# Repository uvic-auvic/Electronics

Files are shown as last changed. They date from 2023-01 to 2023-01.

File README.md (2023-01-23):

# Electronics
Repo containing schematics, pcb, gerber, and other documents for the Electrical Team.

# Directories

## Getting Started
Simple projects meant to introduce members to hardware design

## Submarine
Contains revisions and files for PCBs meant for the Submarine

## Test Equipment
Projects involving test equipment for the PCBs built for the Submarine.

# How revisions work for the projects
Each project will contain a release and development folder. The release folder will contain the board revision that has been ordered, while the development folder will contain revisions that have not been ordered. 

Revisions will be decided by level of change with regards to schematics and pcbs. PCB layout changes and varients will increment by 0.1 and schematic changes will increment by 1. For example, if the power board required a layout change due to a bad route, then the revisions would go from 1.0 to 1.1 because the schematics remain unchanged. If the schematics requried to be redone due to supply chain issues, then the revisions would go from 1.0. to 2.0.

All project revisions should contain a file outlining the reason for the changes for documentation purposes.

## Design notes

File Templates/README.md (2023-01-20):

# Templates
This folder contains template schematics that are common to many PCBs. To save development time, these schematics can be dragged and dropped into a project and modified as needed.

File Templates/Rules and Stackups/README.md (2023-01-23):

# Rules
This directory contains template rules to order boards from different PCB manufacturuers.

Credit to [Ayberk Özgür](https://github.com/ayberkozgur) for the JLC files.

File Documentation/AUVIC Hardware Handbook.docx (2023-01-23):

# Table Of Contents

Table Of Contents 1

General 3

Finding a part in the component library 3

Connectors 3

Resistors 4

Capacitors 4

Microcontroller 6

Microcontroller selection 6

Supporting Hardware 7

Debug 7

LED 9

Oscillator 9

Power Supply 10

Communications 12

Instructions for Creating a New Altium Project 14

Schematic and PCB file 14

PDF Export 14

Active BOM 14

Github and gitignore 14

PCB Layout 15

ESD Protection 15

CAN Connectors 15

TVS diodes: 15

Best Practices and Design Reviews 18

Schematic 18

PCB 18

Preparing to Order 19

References 20

# General

## Finding a part in the component library

The easiest way to find a part is to search by the AUVIC component ID. When searching by component ID, if there are multiple results, ensure that the latest revision is used. The 1 to 2 digit number after the last hyphen is the revision number. Component IDs listed in this document do not contain the revision number. The number will appear when searching in Altium.

# Connectors

Table 1 shows AUVIC’s standard connectors. It should be used whenever possible. Avoid using terminal blocks unless it benefits the design or the standard connectors are not satisfactory. When placing a parts order for your board, ensure that the other end of any connector used is also added to the order.

Standard Connectors List
Purpose | Description | Digikey Part Number | AUVIC Component ID | Price

Power
Power < 10A | Connector Header Through Hole, Right Angle 4 position 0.118" (3.00mm) | WM1820-ND | CMP-005-0021 | $2.24
Power < 5A | Connector Header Through Hole, Right Angle 2 position 0.118" (3.00mm) | WM1819-ND | CMP-00001 | $1.48
Power < 69A | Connector Header Through Hole, Right Angle 6 position 0.224" (5.70mm) | WM11971-ND | CMP-00049 | $3.50
Power < 92A | Connector Header Through Hole, Right Angle 8 position 0.224" (5.70mm) | WM11972-ND | CMP-00051 | $4.18

Data, Data + Power
2 Pin Data | Connector Header Through Hole, Right Angle 2 position 0.100" (2.54mm) | A33855-ND | CMP-00010 | $2.18
4 Pin Data, 2 Pin Data + Power < 2A | Connector Header Through Hole, Right Angle 4 position 0.100" (2.54mm) | A33860-ND | CMP-005-0029 | $1.63
3 Pin Data | Connector Header Through Hole, Right Angle 2 position 0.100" (2.54mm) | A32563-ND | CMP-00099-4 | $2.05

Table 1: Standard Connectors

# Resistors

1. Use SMD resistors unless absolutely necessary for the design
2. Use 0603 sized resistors for SMD unless the power dissipation requirements are higher. 0603 is small but still easy to solder. If we stick to a standard size, it becomes easier to keep resistors in stock
3. Use only 1% resistors unless a higher precision is required. In a production design, 5% would be used to save money since higher precision resistors cost more. However, since we only build a few boards, the cost savings does not outweigh the disadvantages. If all resistors in a board are the same tolerance, we don’t have to order multiple parts for the same resistance. It also becomes easier to keep resistors in stock.

# Capacitors

1. Use SMD capacitors unless absolutely necessary for the design. When using large capacitors (>100uF), you may choose to place multiple smaller capacitors in parallel instead of placing one large capacitor.
2. It is recommended to use 0603 and 0805 sizes for small value ceramic capacitors like bypass capacitors. Try to use the smaller of the two if you have an option.

Standard Capacitors List
Capacitor | Usage | AUVIC Component ID | Digi-Key PN
1nF Ceramic | Filters | CMP-00018 | 1276-1018-2-ND
150nF Ceramic | Bypass cap, filters | CMP-00020 | 1276-6476-1-ND
100nF Ceramic | Bypass cap, filters | CMP-00000 | 1276-1033-1-ND
1uF Ceramic | Bypass cap, filters | CMP-00005 | 1276-6470-1-ND
4.7uF | Bypass cap, filters | CMP-00019 | 1276-2789-1-ND
10uF Ceramic | Bypass cap, filters | CMP-00004 | 1276-6767-1-ND

Table 2: Standard Capacitors

# Microcontroller

This section details the hardware requirements if using a microcontroller in your design.

## Microcontroller selection

AUVIC has moved to using the same microcontroller for all designs with a few exceptions. This was done in an effort to simplify firmware development. The STM32F413xG has been determined to be the best controller to use. The table 3 lists the variants you can choose from for your design. ST provides an 81-pin package, but due to the complexity of the footprint, this variant should not be used for new designs.

Microcontroller List

General Purpose
MFG PN | Description | AUVIC Component ID | Digi-Key PN
STM32F413VGT6 | 100-pin LQFP, 1Mbyte Flash 320KB RAM 100 MHz CPU | CMP-00007
STM32F413RGT6 | 64-pin LQFP, 1Mbyte Flash 320KB RAM 100 MHz CPU | CMP-00006
STM32F413ZGT6 | 144-pin LQFP, 1Mbyte Flash 320KB RAM 100 MHz CPU

Special Purpose
STM32F429VGT6 | For high performance or special peripheral requirements only 100-pin LQPF, 1Mbyte Flash 256+4KB RAM 180 MHz CPU | CMP-00008
~~STM32F042F4P6TR~~ | ~~For simple boards only.~~ ~~32-bit 48MHz 16kB (16k x8) Flash 20-TSSOP~~ | | ~~497-19320-1-ND~~

Table 3: List of approved microcontrollers

## Supporting Hardware

### Debug

All boards need to have a debug header that will connect to a ST debugger. This is how we flash new firmware to the boards and attach a debugger to step through code. The header also has UART for debugging which must be connected to UART capable pins on the microcontroller. It is recommended to connect RX to PD9 and TX to PD8 since these pins are connected to the ST-Link VCP pins on the Nucleo board. However, this is not a hard requirement. Note that the SWCLK, SWDIO, SWO, and NRST connect to specific pins on the STM microcontroller you are using (check the datasheet to make sure you are connecting to the right pin). The 5V pin must be connected to the board’s internal 5V through a schottky diode. This allows the debugger to power the microcontroller. See figure 1 and table 4 for reference.

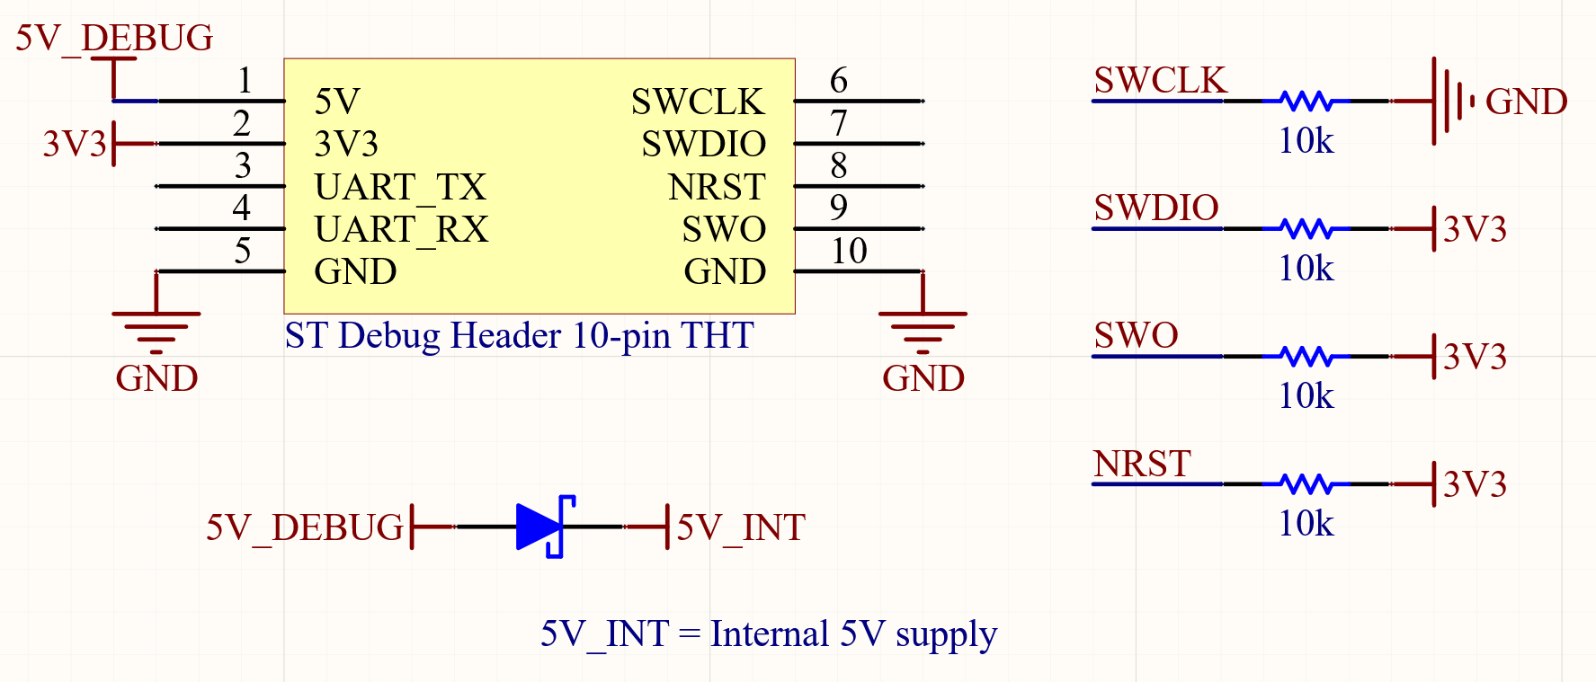
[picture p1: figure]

Figure 1: Microcontroller debug header schematic

Part | AUVIC Component ID
Header THT | CMP-00011
Header SMD | CMP-00013
Schottky Diode | CMP-057-0000
10kR Resistor | CMP-047-0013-1

Table 4: Microcontroller debug header component list

Another debug feature that all boards will have to incorporate are reset buttons to manually reset the STM microcontroller, and a boot header that allows the user to force the STM microcontroller into boot mode. See figure 2 and table 5 for reference.

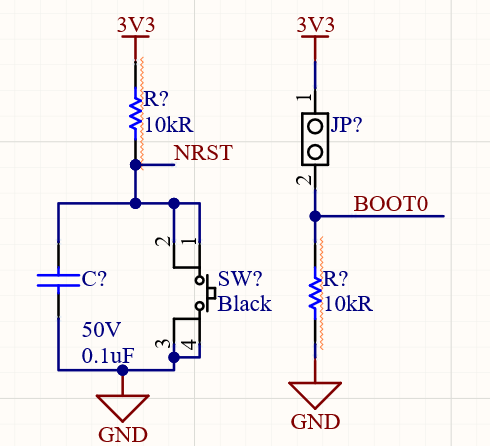
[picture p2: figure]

Figure 2: Microcontroller External Reset and Boot Schematic

Part | AUVIC Component ID
Switch SMD (option 1) | CMP-00077-1
0.1uF Capacitor | CMP-00000-3
2 pin Header | CMP-004-0001-1
10kR Resistor | CMP-047-0013-1
CMP-00104-1 (option 2) | CMP-00104-1

Table 5: Microcontroller External Reset and Boot component list

### LED

LEDs should be connected to the microcontroller’s GPIOs to help with debugging. The more LEDs the better, but 3 is the recommended number. It is recommended to connect the LEDs to PB0(green), PB7(blue), and PB14(red) since these pins are connected to LEDs on the Nucleo board. However, this is not a hard requirement. Use one red LED, one green LED and one blue LED. The table below shows the LED part number and recommended resistor values.

Part | AUVIC Component ID | Forward Voltage | Recommended Resistor, IF=4mA
| | | Vin = 3.3V | Vin = 5V | Vin = 12V | Vin = VBatt
Red LED | CMP-00066 | 2V | 330Ω | 750Ω | 2.49kΩ | 6.49kΩ
Green LED | CMP-00064 | 2.85V | 110Ω | 536Ω | 2.26kΩ | 6.34kΩ
Blue LED | CMP-00063 | 2.85V | 110Ω | 536Ω | 2.26kΩ | 6.34kΩ
Orange LED | CMP-00065 | 2V | 330Ω | 750Ω | 2.49kΩ | 6.49kΩ

Table x: LED component list and recommended resistor value

### Oscillator

If your design requires an accurate clock, you must add the circuit below to your schematic. For example, the motor controller’s RPM feedback requires an accurate clock because it compares the time between two rising edges of the motor back emf. However, if your board has space it is always recommended to add this so that the option of enabling it later is available. See figure 3 and table 5 for reference.

Part | AUVIC Component ID
8 Mhz Oscillator | CMP-00079-2
16pF Cap | CMP-00087-2

Table 5: Microcontroller oscillator component list

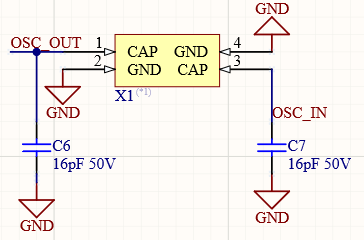
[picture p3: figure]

Figure 3: Microcontroller external oscillator schematic

### Power Supply

The STM microcontrollers can operate with a supply voltage of 1.8V to 3.6V [1]. AUVIC’s designs should operate the controllers using a 3.3V supply. It is recommended to use a 3.3V linear regulator with a input voltage of 5V. See figure X and table X for reference. All boards should take 5V from the power board’s 5V rail.

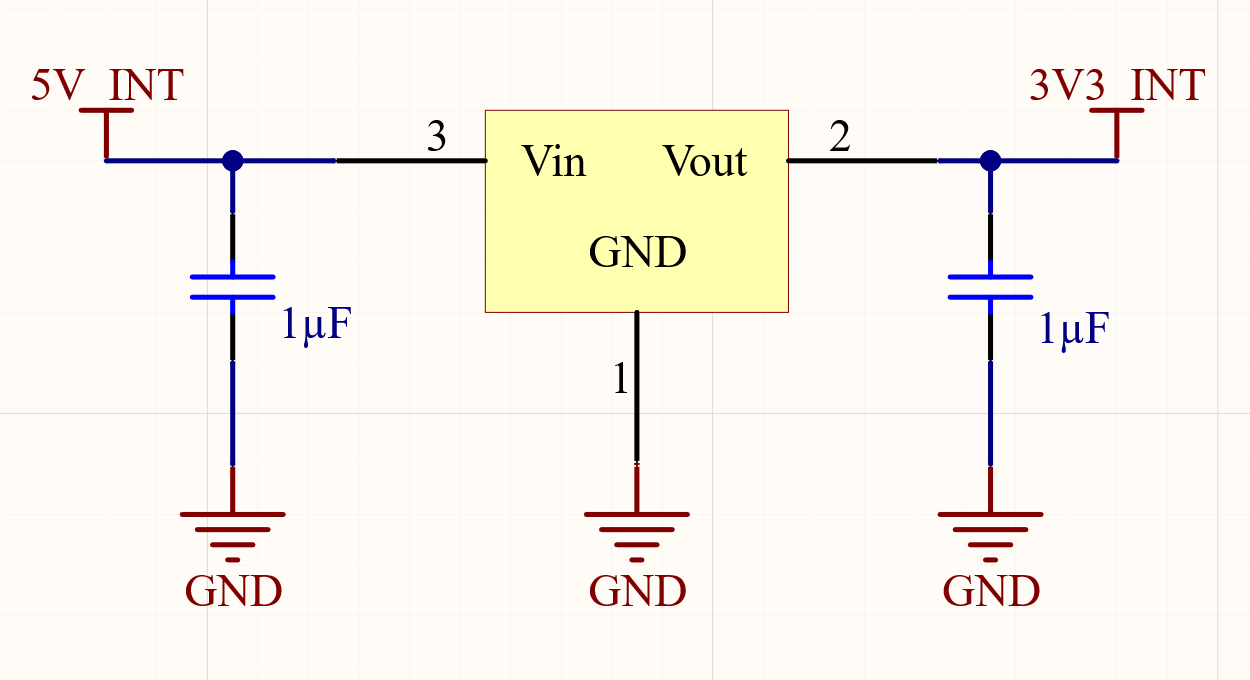
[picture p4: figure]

Part | AUVIC Component ID
LDO | CMP-00003
1uF Cap | CMP-00005

Table x: Component list for 3V3 rail

Figure x: Schematic for 3V rail

Appropriate bypass capacitors must be used.

- One 10uF ceramic or tantalum capacitor per chip
- One 0.1uF ceramic capacitor per VDD pin
- If VBAT is not being supplied by a separate battery, it should be connected to VDD with a 0.1uF ceramic decoupling capacitor. This will be the case for AUVIC’s boards unless we build a board with a built in battery.
- One 0.1uF and one 1uF ceramic capacitor per VDDA pin. 3.3V should be connected to the VDDA/VREF+ pin through a ferrite bead
- One 2.2uF low ESR ceramic capacitor per VCAP pin. There should be two VCAP pins. This is required if using the internal regulator on the microcontroller which is the case for AUVIC’s designs.

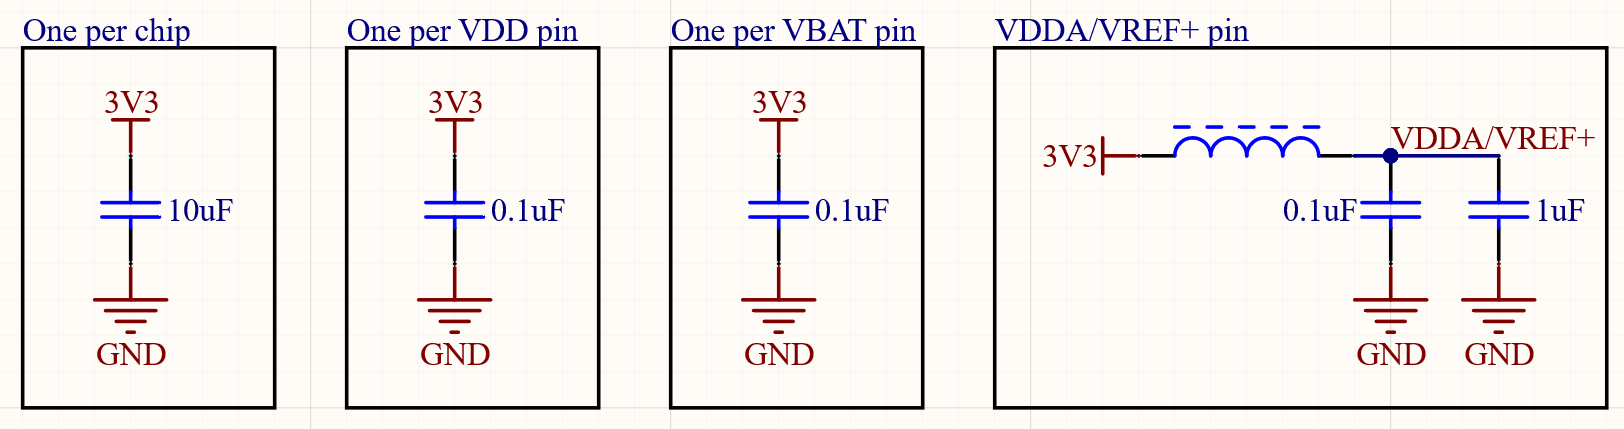
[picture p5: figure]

Figure xa: Microcontroller bypass capacitor schematic

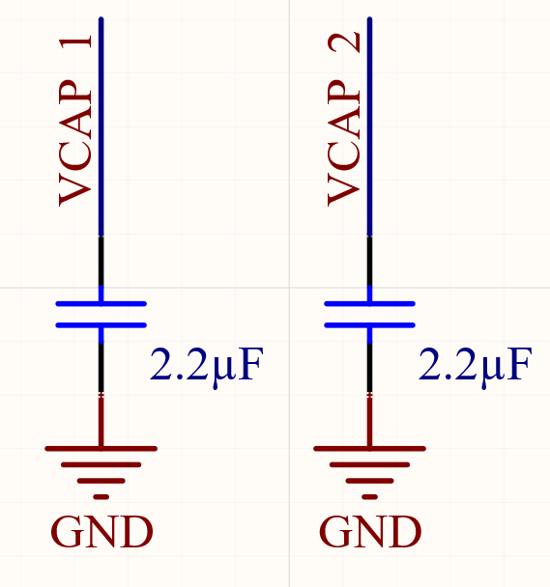
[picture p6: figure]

Part | AUVIC Component ID
0.1uF Cap | CMP-00000
1uF Cap | CMP-00005
10uF Cap | CMP-00004
Ferrite bead | CMP-00016
2.2uF Cap | CMP-006-0030

Table x: Microcontroller bypass capacitor component list

Figure xb: Microcontroller bypass capacitor schematic

For a more detailed explanation on the power supply requirements of the STM32F4 series microcontrollers, read cited text number 1.

## Communications

All AUVIC controllers will use CAN to communicate. CAN 2.0 operating at 500kbps will be used. See figure x for a reference design. The CAN_H and CAN_L lines must have a differential pair directive added in Altium to ensure the trace length on the PCB are the same. The CAN_TX and CAN_RX pins should be connected to CAN capable pins on the microcontroller. Choose CAN1 or CAN2 if possible. The CAN_STB pin should connect to a GPIO on the microcontroller. The 120Ω terminating resistor should be present in your schematic, but should only be populated if your component will be terminating the CAN bus. There will only be two devices per bus at either end of the bus. The TVS diode should be present in your schematic, but should not be populated unless deemed necessary after testing.

Note: This circuit is still under test and could change. A TVS diode and common mode choke might be added. Any board that uses this design should not be fabricated until this circuit has completed the required testing.

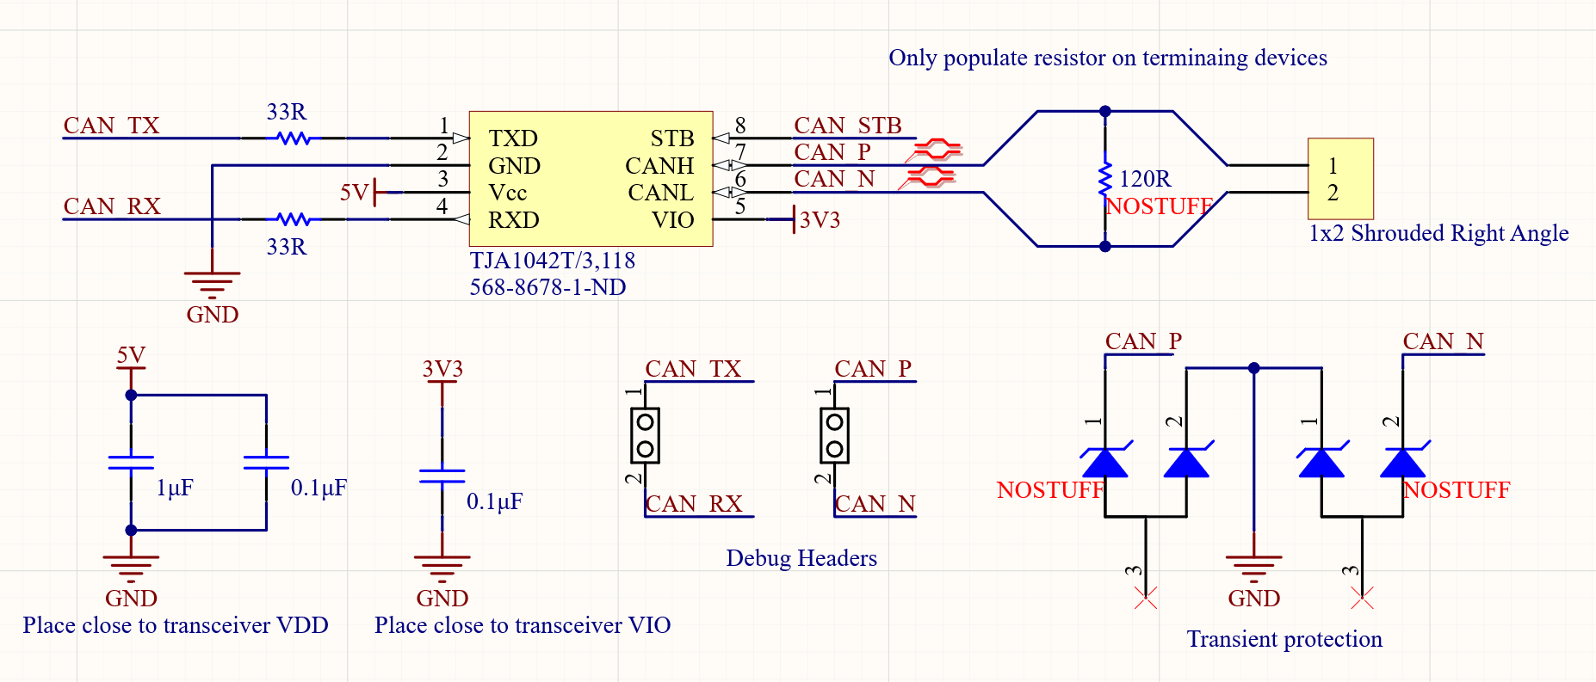
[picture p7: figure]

Figure x: CAN transceiver reference schematic

Part | AUVIC Component ID
CAN Transceiver | CMP-032-0000
2-pin Connector | CMP-00010
2-pin Header | CMP-004-0001
TVS Diode | CMP-058-0000
0.1uF | CMP-00000
1uF | CMP-00005
120 Ohm Resistor | CMP-00061
33 Ohm Resistor | CMP-00060

Table x: CAN transceiver schematic component list

# Instructions for Creating a New Altium Project

## Schematic and PCB file

## PDF Export

Use the same .OutJob file for everything. Naming convention.

## Active BOM

Currency, supplier part number under one column.

## Github and gitignore

Blah

Don’t upload history and project output files

# PCB Layout

The following sections will give recommendations for PCB layouts.

## ESD Protection

Electrostatic Discharge is the sudden flow of electricity between two charged objects. Testing for ESD on a prototype PCB requires the use of an ESD Gun, however these are expensive. The following subsections provide layout tips to lower the occurrence of ESD.

### CAN Connectors

AND8169/D EMI/ESD Protection Solutions for the CAN Bus by ON Semiconductor gives the following guidelines on ESD protection:

1. Locate the protection devices (TVS or diode) as close as possible to the I/O connector. This absorbs transient voltage before it couples to adjacent traces.
2. Minimize the loop area for the high-speed data lines, power and ground lines to reduce the radiated emissions and RF noise.
3. Minimize path length between CAN signal lines and protective devices.
4. Use ground planes whenever possible to reduce parasitic capacitance and inductance.

### TVS diodes:

Protects a transceiver by clamping a surge voltage to a safe level.

  - Pros: High Z below breakdown voltage and low Z above breakdown voltage. Optimized to absorb peak energy of transient voltages.
  - Cons: May clamp the CAN_L and CAN_H waveforms if a common mode or offset voltage exists.
  - Chosen TVS diode: PESD36VS2UT

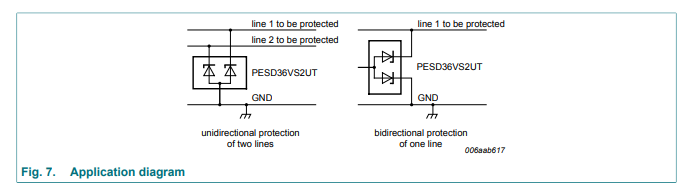
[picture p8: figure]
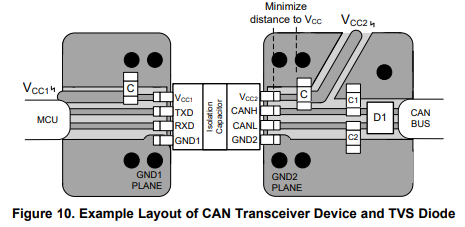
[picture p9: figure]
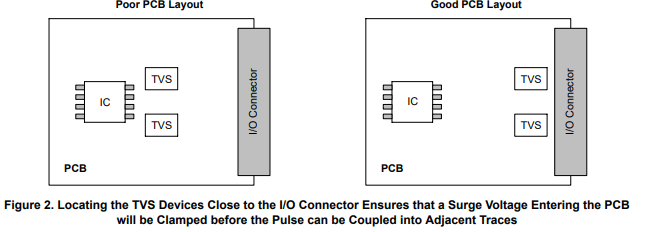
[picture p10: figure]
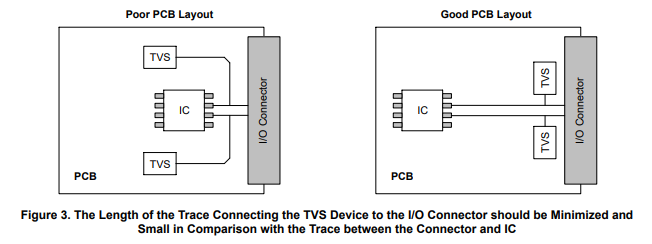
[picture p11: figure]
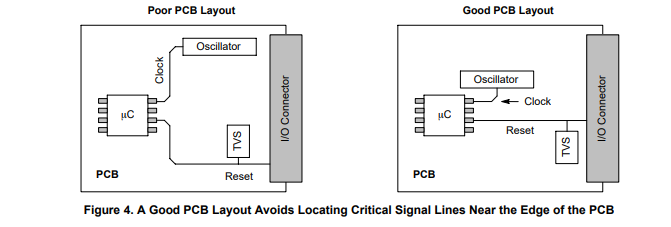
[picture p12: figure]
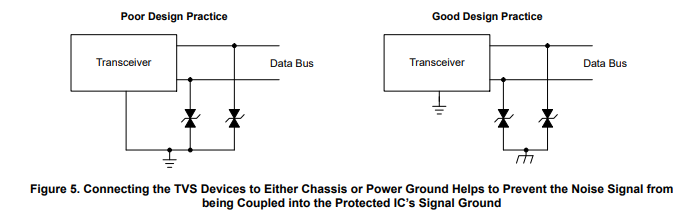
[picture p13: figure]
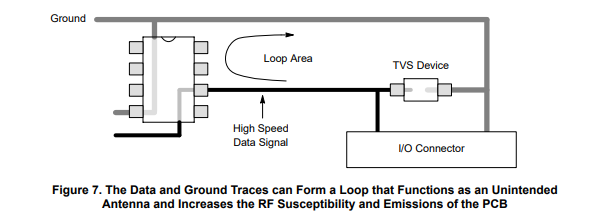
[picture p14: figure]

# Best Practices and Design Reviews

## Schematic

1. Be wary of logic levels on STM32 (5V tolerant etc)
2. Ensure correct resistors for LEDs

## PCB

4. Make sure vias are not directly under silkscreen designators or they will not print correctly
5. Use lower density component footprints
6. Double check bypass cap requirements for ICs
7. Place connectors at edge of board oriented away from center of board
8. Place designators so that when letters are upright the corresponding component is below
9. Vias: tent all vias and set to direct connect in thermal relief
10. Remove unnecessary bends in traces

https://www.ti.com/lit/an/szza009/szza009.pdf?ts=1610821093742&ref_url=https%253A%252F%252Fwww.google.com%252F

https://www.allaboutcircuits.com/technical-articles/practical-pcb-layout-tips/

https://www.allaboutcircuits.com/technical-articles/common-layer-stack-ups-for-a-four-layer-board/

https://resources.altium.com/p/top-5-pcb-design-guidelines-every-pcb-designer-needs-know

The above are good resources for PCB best practices

Set Design rules to the following:

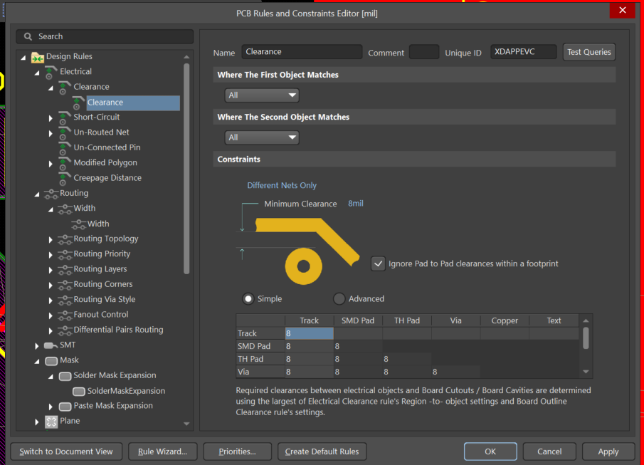
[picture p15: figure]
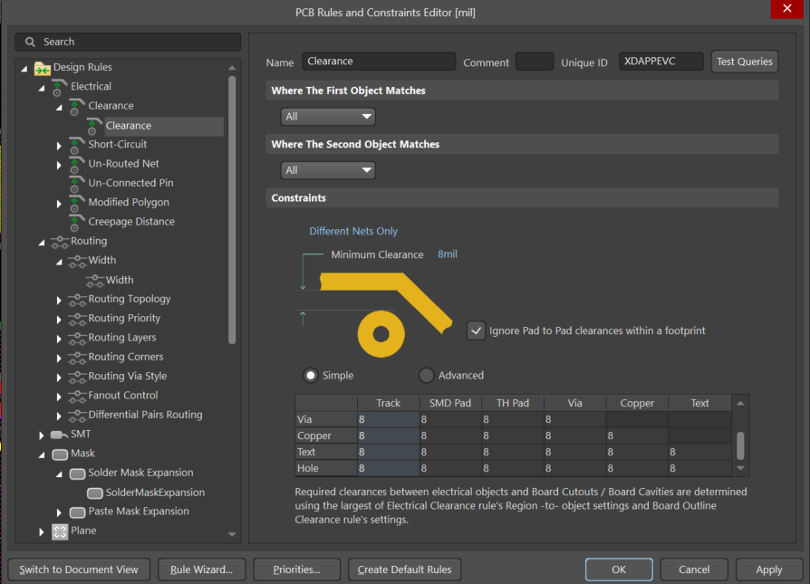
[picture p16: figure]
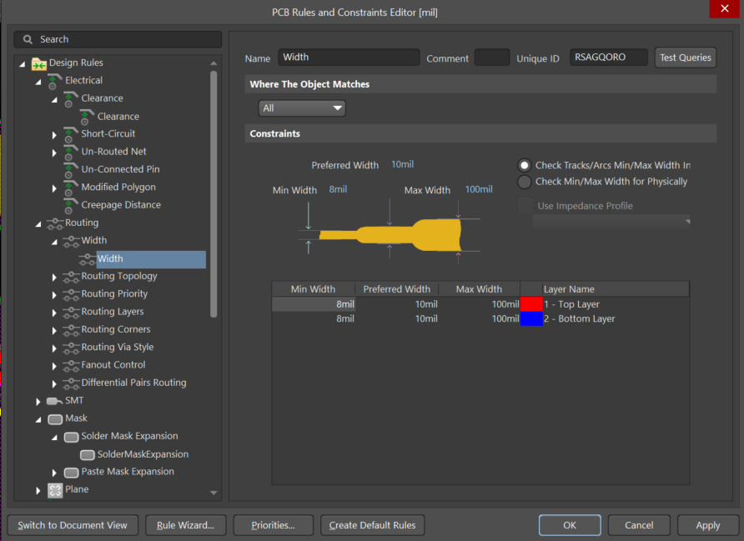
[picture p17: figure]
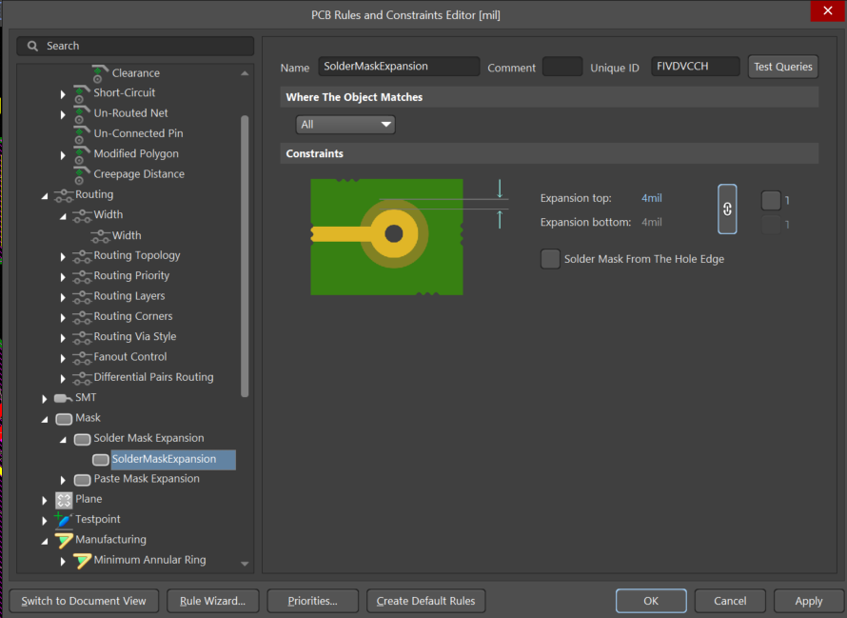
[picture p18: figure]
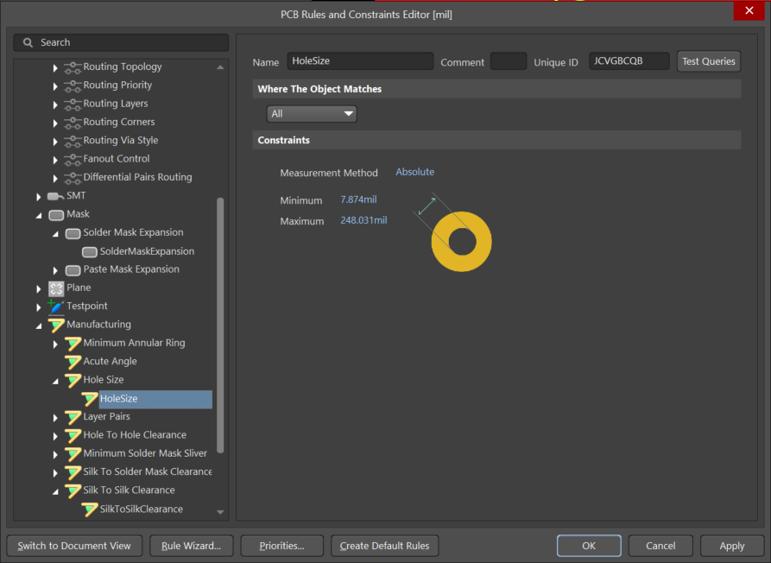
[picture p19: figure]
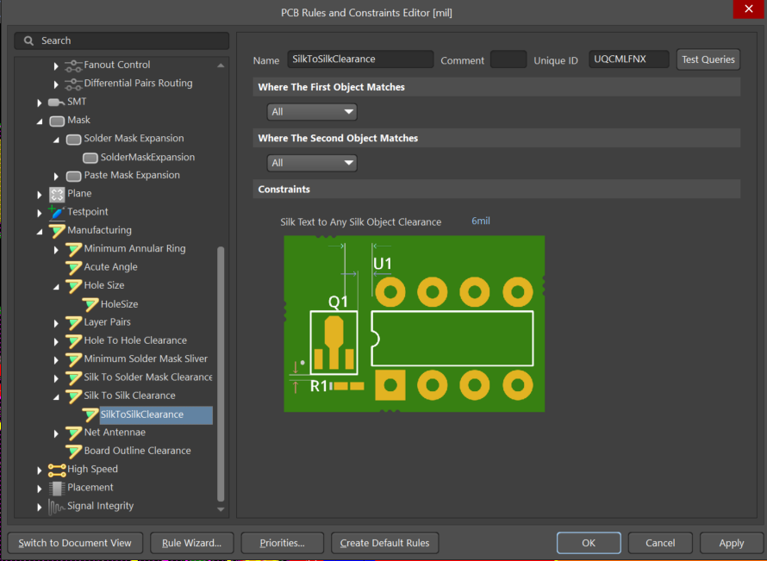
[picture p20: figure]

# Preparing to Order

1. Make a keepout layer
  a. Go to Keepout Layer (bottom tab)
  b. Draw lines around board edge
  c. Ensure polygon pours are in line with or greater than keepout area and repour
2. Open Settings folder-> Open Output Job Files -> Open PCBname.OutJob
3. Add New Output Container
  a. New Folder Structure
  b. Name it “Fabrication”
4. In Fabrication Outputs
  a. Add Gerber and NC Drill files and configure(by double clicking) based on instructions here: https://support.jlcpcb.com/article/42-how-to-export-altium-pcb-to-gerber-files
  b. *ignore drill drawing tab
5. Click enabled and link to Fabrication Folder
6. Add New Output Container
  a. New Folder Structure
  b. Name it “Step”
7. In Export Outputs
  a. Add Step file
8. Click enabled and link to Step Folder
9. Add New Output Container
  a. New Folder Structure
  b. Name it “BOM”
10. In Report Outputs
  a. Add Project BOM
11. Click enabled and link to Report Folder
12. Click generate content in all output containers

# References

[1] https://www.st.com/resource/en/application_note/dm00115714-getting-started-with-stm32f4xxxx-mcu-hardware-development-stmicroelectronics.pdf

[2]

https://assets.nexperia.com/documents/data-sheet/PESD36VS2UT.pdf

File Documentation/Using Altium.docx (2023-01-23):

# Using Altium

Work in Progress. The idea of this document is every time you have to look something up or figure out something with regards to using Altium, throw it in this document. In my opinion, Altium’s online documentation is pretty confusing and hard to follow. For example, they would say “do x from menu y” without explaining how to get to menu y. Because of this, we have this document to lay out how to do things in Altium outlined as simply as possible.

1. Shortcuts 1

2. Renewing the Team Altium License 1

2.1 Example Application Form 2

3. Schematic to PCB 4

Revision History 6

# 1. Shortcuts

Key Combination | Action
p | Open Place menu
j | Open find menu
Click on part of track then tab | Selects entire track
Ctrl+shift+scroll wheel | Change layers
Shift+Spacebar (while making polygon) | Change corner type

# 2. Renewing the Team Altium License

Author: Rob Keen

Must be done annually around the beginning of November. Complete the form at https://www.altium.com/solutions/academic-programs/team-sponsorships and you should get an email from Altium a few days later (method as of November 8th, 2021).

Important Note: Make sure the email in the registration form is one that is registered under an administrator in the Altium dashboard (https://dashboard.live.altium.com). This way, the existing license will get updated instead of needing to make a completely new workspace. If the existing workspace does not get updated, reach out to Altium. Can be checked through the above linked Altium dashboard.

University address for easy copy-pasting: 3800 Finnerty Rd, Victoria, CA V8P 5C2

## 2.1 Example Application Form

The following is an example completed form that resulted in a successful Altium sponsorship:

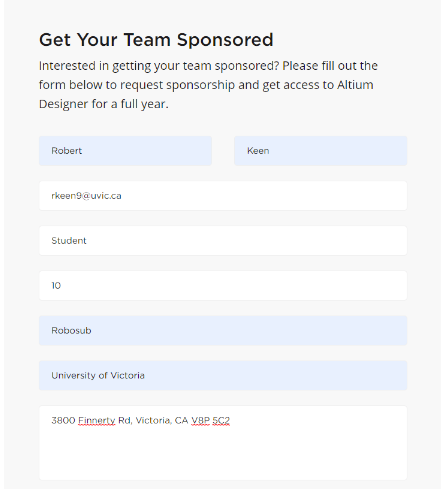
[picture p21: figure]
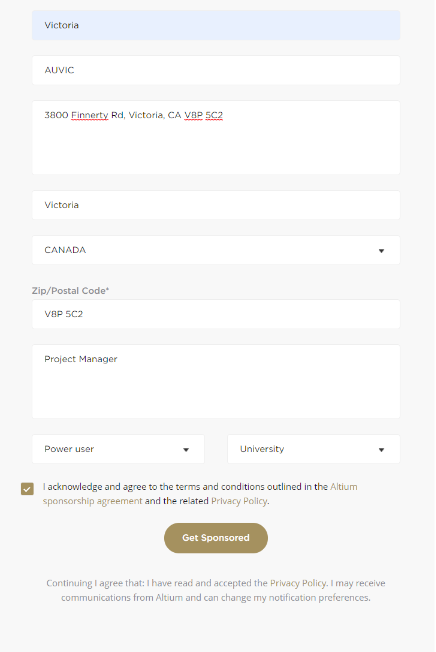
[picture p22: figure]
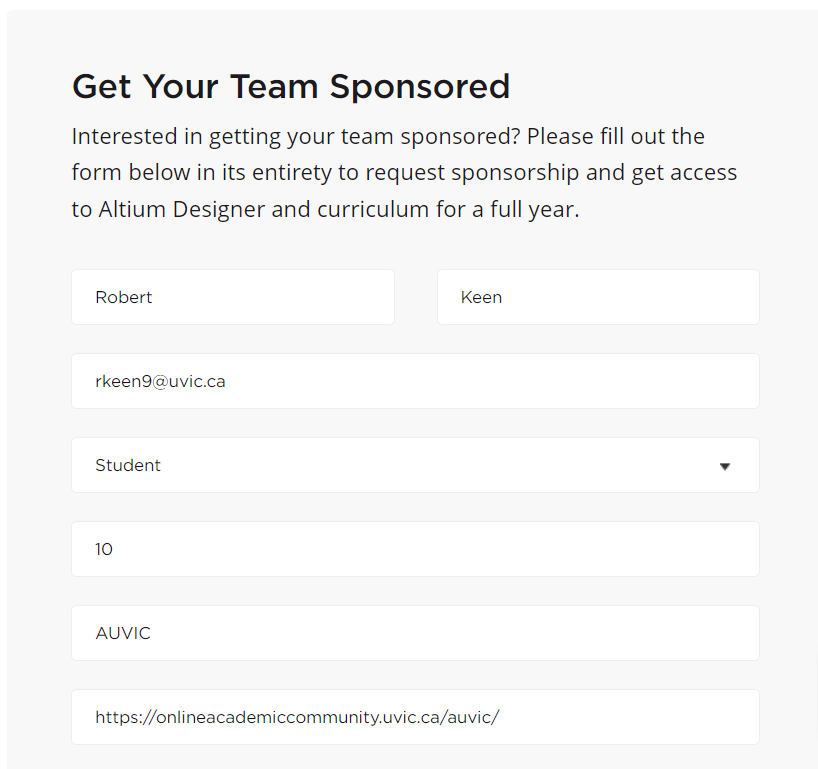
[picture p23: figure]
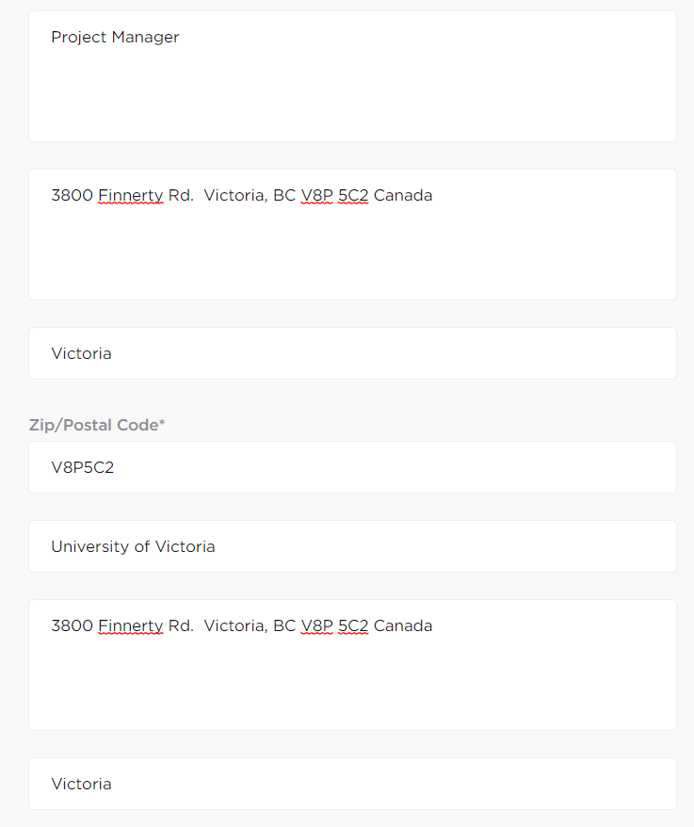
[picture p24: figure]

# 3. Schematic to PCB

Author: Rob Keen

1. Create new .PcbDoc file by right clicking on the project in the projects tab and choosing “Add New to Project>PCB”


2. Enter the new document, save with ctrl+s, and name the file whatever you want
3. “Design>Import changes From filename.PrjPcb”


4. From the Engineering Change Order window that appears, “Validate Changes” and address any errors that come up  Note: the above error can be safely ignored


5. Once errors are addressed click “Execute Changes”
6. You are now ready for routing

# 4. Differential Pair Routing

Author: Rob Keen

Sources: https://www.altium.com/documentation/altium-designer/pcb-dlg-managediffpairsformcreate-differential-pairs-from-nets-ad

## 4.1 Getting to the Differential Pair Editor

1. With the .PcbDoc file open, show the PCB panel by clicking “View>Panels>PCB”


2. Open the PCB panel, click the drop down menu at the top (by default it says “Nets”) and choose “Differential pairs Editor”


# Revision History

Name | Date | Revision Details
Robert Keen | Nov. 8, 2021 | Initial release
Robert Keen | Nov. 20, 2021 | Converted this document into a generic using Altium document

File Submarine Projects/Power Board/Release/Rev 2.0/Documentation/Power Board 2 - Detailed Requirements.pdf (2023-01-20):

## Overview

The Autonomous Underwater Vehicle Interdisciplinary Club (AUVIC) competes in an annual international competition where teams build autonomous underwater vehicles (AUVs) to complete an underwater obstacle course. AUVIC is in need of a new power and battery management board(PMB) for the 2021 Autonomous Underwater Vehicle (AUV).

## Specifications

The new PMB is divided into four subsections. The requirements for each subsection are outlined in the following sections.

## 3.1 Battery Management

The following specifications were established by AUVIC for the battery management section of the power board:
1. Should have a input voltage range of 18V to 28V.
2. Should use two 6 cell LiPo batteries as its power source.
3. Should have the ability to run the two batteries in parallel.
4. Each battery should have fuses. Regular sized automotive fuses are recommended.
5. Should have LEDs to indicate if the battery is connected.
6. Should have the ability to monitor battery pack voltage, individual cell voltage and pack current.

## 3.2 Power Distribution

The following specifications were provided by AUVIC for the power distribution section of the PMB:
1. Should have the following power outputs for external systems:
1.1. 5V at 8A.
1.1.1. LCD board - 4A*
1.1.2. Inertial Measurement Unit (IMU) - 500mA
1.1.3. Hydrophones - 250mA*
1.1.4. Torpedo 5V electronics - 250mA*
1.1.5. Motor controller 5V electronics - 250mA*
1.1.6. Buffer for unplanned boards - 2.75A
1.2. 12V at 8A.
1.2.1. Doppler Velocity Log (DVL) - 3A
1.2.2. Ball dropper and grabber arm - 3A*
1.2.3. Buffer for unplanned boards - 2A
1.3. 16V at 3A.
1.3.1. Nvidia Jetson TX2 and peripherals - 3A
1.4. VBatt (22.2V nominal) at 60A continuous.

1

1.4.1. Motor controller - 60A peak
1.4.2. Torpedo launcher - 30A for < 1s
2. Should be able to switch on/off all external power using the microcontroller.
3. Should have the ability to monitor current for each external power output.
4. Should have LEDs at each output to indicate if the output is on or off.
5. Should have fuses at each output. Regular sized automotive fuses are recommended.
* Estimated values.

## 3.3 Microcontroller & Communication

The following specifications were provided by AUVIC for the microcontroller and communication section of the power board:
1. Should use a STM32F413 microcontroller.
2. Should have a RS232 transceiver to communicate with an IMU.
3. Should have LEDs connected to the microcontroller for debugging and to show system status.
4. Should use a Controller Area Network (CAN) bus to communicate to external systems.

## 3.4 Sensors

From AUVIC, the following requirements were given for the sensors section of the power board:
1. Should connect to a reed switch to power on/off the AUV.
2. Should connect to a water sensor to detect leaks in the vehicle’s housing.
3. Should measure internal pressure, temperature, and humidity.
4. Should connect to an external water pressure sensor used to determine the AUV’s depth in the water.

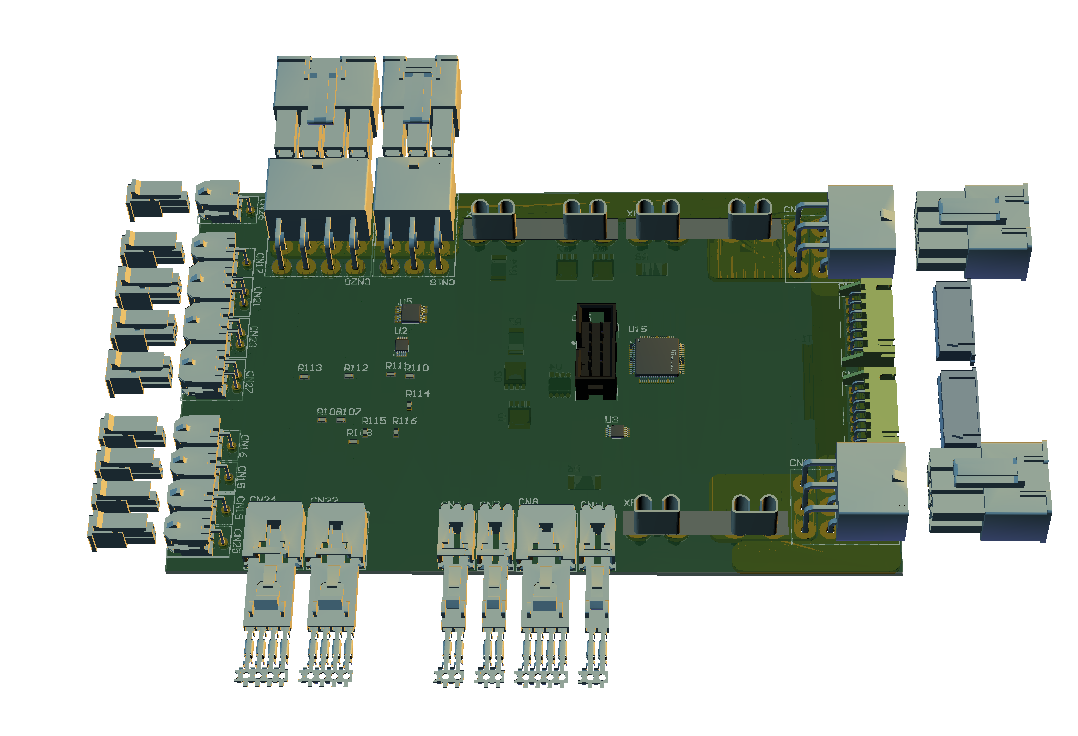
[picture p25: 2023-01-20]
Submarine Projects/Power Board/Release/Rev 2.0/3D Model/Power_Board_2.png

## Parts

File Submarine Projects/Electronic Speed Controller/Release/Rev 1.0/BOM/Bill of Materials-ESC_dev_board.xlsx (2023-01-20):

Line # | Name | Description | Designator | Revision ID | Revision State | Quantity | Manufacturer 1 | Manufacturer Part Number 1 | Manufacturer Lifecycle 1 | Supplier 1 | Supplier Part Number 1 | Supplier Unit Price 1 | Supplier Subtotal 1
 | 1μF | Capacitor, Ceramic, 50V, +/- 10%, 0603 SMD, X5R | C5 |  | Not managed | 1 | Samsung | CL10A105KB8NNNC | Volume Production | Digi-Key | 1276-1860-1-ND | 0.17 | 0.17
 | 0.1uF, 50V, 10%, X7R, 0603 | 0.1µF ±10% Ceramic Capacitor X7R 0603 (1608 Metric) | C6 |  | Not managed | 1 | TDK | C1608X7R1H104K | Not Recommended for New Design | Digi-Key | 445-1314-1-ND | 0.12 | 0.12
 | 100µF | 100µF 35V Aluminum Polymer Capacitor Radial, Can - SMD 30mOhm 2000 Hrs @ 105°C | C7, C8, C9, C10 |  | Not managed | 4 | Wurth Electronics | 875115652007 | Unknown | Digi-Key | 732-11942-1-ND | 2.76 | 11.04
 | Header Male 1x4 | 1x4, Pads Pitch: 0.1" (2.54mm), Through hole | CN3, CN4 |  | Not managed | 2 | Harwin | M20-9990446 | Volume Production | Digi-Key | 952-2266-ND | 0.19 | 0.38
 | 3x1, Terminal Block, Pitch: 5mm, Screw, THT | 3x1, Terminal Block, Pitch: 5mm, Screw, THT | CN5 |  | Not managed | 1 | Phoenix Contact | 1935174 | Volume Production | Digi-Key | 277-1578-ND | 0.6 | 0.6
 | 2x1 Term Block |  | J3 |  | Not managed | 1 | Phoenix Contact | 1935776 | Volume Production | Digi-Key | 277-6405-ND | 0.49 | 0.49
 | SI7625DN-T1-GE3 | P-Channel 30V 35A (Tc) 3.7W (Ta), 52W (Tc) Surface Mount PowerPAK® 1212-8 | Q1, Q2, Q3 |  | Not managed | 3 | Vishay Siliconix | SI7625DN-T1-GE3 | Volume Production | Digi-Key | SI7625DN-T1-GE3CT-ND | 1.07 | 3.21
 | SIS476DN-T1-GE3 | N-Channel 30V 40A (Tc) 3.7W (Ta), 52W (Tc) Surface Mount PowerPAK® 1212-8 | Q4, Q5, Q6 |  | Not managed | 3 | Vishay | SIS476DN-T1-GE3 | Volume Production | Digi-Key | SIS476DN-T1-GE3CT-ND | 1.12 | 3.36
 | 0R | 0R, 1%, 1/10W, 0603 SMD | R3, R4, R5, R6, R7, R8 |  | Not managed | 6 | Yageo | RC0603JR-070RL | Volume Production | Digi-Key | 311-0.0GRCT-ND | 0.019 | 0.19
 | 0.01 | RES 0.01 OHM 1% 3W 2512 | R9 |  | Not managed | 1 | Bourns | CRA2512-FZ-R010ELF | Unknown | Digi-Key | CRA2512-FZ-R010ELFCT-ND | 0.69 | 0.69
 | A4963 | A4963, BLDC, 3 Phase, Sensorless | U3 |  | Not managed | 1 | Allegro MicroSystems | A4963GLPTR-T | Volume Production | Digi-Key | 620-1686-1-ND | 2.7 | 2.7

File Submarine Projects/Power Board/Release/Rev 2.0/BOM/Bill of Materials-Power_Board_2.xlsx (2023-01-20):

Line # | Name | Description | Designator | Quantity | Manufacturer 1 | Manufacturer Part Number 1 | Manufacturer Lifecycle 1 | Supplier 1 | Supplier Part Number 1 | Supplier Unit Price 1 | Supplier Subtotal 1
 | CL10B104JB8NNNC | CAP CER 0.1UF 50V X7R 0603 | C1, C2, C3, C4, C5, C6, C8, C16, C22, C23, C32, C38, C39, C41, C42, C47, C49, C50, C51, C53, C60, C64, C66, C67, C68, C69, C70, C71, C74, C75, C76, C77, C78, C79, C80, C81, C82, C83, C84, C85, C86, C87, C88, C89 | 44
 | CL31B106KBHNNNE | Cap Ceramic 10uF 50V X7R 10% Pad SMD 1206 125°C T/R | C7, C24, C25, C26, C27, C40, C46, C52, C72 | 9
 | CL31B475KBHNNNE | Capacitor 4.7 uF 50 VDC PU=2000 ST, CL31B475KBHNNNE, Samsung | C9, C10, C21, C37 | 4 | Samsung | CL31B475KBHNNNE | Volume Production | Digi-Key | 1276-2789-1-ND | 0.38374 | 1.53
 | 470nF, 50V, 10%, 0603, Ceramic, SMD | Capacitor, Ceramic, 50V, 10%, 0603 SMD, X7R | C11, C28 | 2 | TDK | C1608X7R1H474K080AC | Volume Production | Digi-Key | 445-5952-6-ND | 0.26256 | 0.52512
 | CL10B102KB8NNNC | Cap Ceramic 0.001uF 50V X7R 10% Pad SMD 0603 125°C T/R | C12, C18, C29 | 3
 | GRM188R60J226MEA0D | MURATA - GRM188R60J226MEA0D - SMD Multilayer Ceramic Capacitor, 22 µF, 6.3 V, 0603 [1608 Metric], ± 20%, X5R, GRM Series | C13, C14, C19, C20 | 4
 | CL10C101FB8NNNC | Ceramic capacitor SMD 0603 100 pF 50 V 1 % | C15 | 1
 | CL21B154KBFNNNG | CAP CER 0.15UF 50V X7R 0805 | C17, C33 | 2
 | GRM1885C2A271JA01D | CAP CER 270PF 100V C0G/NP0 0603 | C30 | 1
 | C3216X5R1E476M160AC | TDK - C3216X5R1E476M160AC - SMD Multilayer Ceramic Capacitor, 47 µF, 25 V, 1206 [3216 Metric], ± 20%, X5R, C Series | C31, C35, C36 | 3
 | CGA4C2C0G1H272J060AA | CAP CER 2700PF 50V C0G 0805 | C34 | 1
 | GRM32ER71E226ME15K | CAP CER 22UF 25V X7R 1210 | C43, C44, C48 | 3
 | CL21B105KBFNNNG | SAMSUNG ELECTRO-MECHANICS - CL21B105KBFNNNG - MLCC CAPACITORS | C45, C65, C73 | 3
15 | 0.015uF 50V 0603 SMD, Ceramic | Capacitor, Ceramic, 50V, +/-10%, 0603 SMD, X7R | C54 | 1
2 | 4.7uF 50V 1206 SMD, Ceramic | Capacitor, Ceramic, 50V, +/- 10%, 1206 SMD, X7R | C55 | 1
5 | 1uF 25V 0603 SMD, Ceramic | Capacitor, Ceramic, 25V, +/- 10%, 0603 SMD, X5R | C56, C57 | 2 | Murata | GRM188R61E105KA12D | Volume Production | Digi-Key | 490-3897-1-ND | 0 | 0
4 | 0.1uF, 50V, 10%, X7R, 1608 | CAP CER 0.1UF 50V 10% X7R 1608 (0603) | C58 | 1 | Samsung | CL10B104KB8SFNC | Volume Production | Digi-Key | 1276-1936-1-ND | 0.10098 | 0.10098
6 | 10uF 10V 0805 SMD, Ceramic | Capacitor, Ceramic, 10V, +/- 10%, 0805 SMD, X5R | C59 | 1 | Murata | GRM219R61A106KE44D | Not Recommended for New Design | Digi-Key | 490-4735-1-ND | 0 | 0
 | 16pF Ceramic 50V 5% 0603 | Cap Ceramic 16pF 50V C0G 5% SMD 0603 125C Paper T/R | C61, C62 | 2
 | 2.2uF, 50V, 0603 SMD, X5R, Ceramic | Capacitor, Ceramic, 50V, 10%, 0603 SMD, X5R | C63 | 1 | Murata | GRM188R61H225KE11D | Volume Production | Digi-Key | 490-10733-6-ND | 0.38374 | 0.38374
 | 76825-0006 | CONNECTOR, HEADER, 6POS, 2ROW, 5.7MM; Product Range:Mega-Fit 76825 Series; Contact Termination Type:Through Hole; Gender:Header; No. of Contacts:6; Pitch Spacing:5.7mm; Contact Plating:Tin Plated Contacts; Contact Material:Copper | CN1, CN2, CN18 | 3 | Molex | 76825-0006 | Volume Production | Digi-Key | WM11971-ND | 2.39 | 7.18
 | S7B-XH-A(LF)(SN) | CONN HEADER XH SIDE 7POS 2.5MM | CN3, CN4 | 2 | JST | S7B-XH-A(LF)(SN) | Volume Production | Digi-Key | 455-2240-ND | 0.45443 | 0.90886
 | ST Debug Header 10-pin THT | CONN HEADER VERT 10POS 2.54MM | CN5 | 1 | Sullins | SBH11-PBPC-D05-ST-BK | Volume Production | Digi-Key | S9169-ND | 0.42413 | 0.42413
 | 1x2 Shrouded Right Angle | 02 MTE HDR SRRA LATCH | CN6, CN7, CN11 | 3 | TE Connectivity | 5-104935-5 | Volume Production | Digi-Key | A33855-ND | 1.47 | 4.42
 | Header, Male, 1x4, RA, Pitch 0.1" (2.54mm) | Connector Header Through Hole, Right Angle 4 position 0.100" (2.54mm) | CN8, CN22, CN24 | 3 | TE Connectivity | 5-104935-1 | Volume Production | Digi-Key | A33860-ND | 1.65 | 4.94
 | Header, Female, 1x2, Right Angle, Pitch 0.118" (3.00mm), THT | Connector Header Through Hole, Right Angle 2 position | CN15, CN16, CN17, CN19, CN25, CN26 | 6 | Molex | 43045-0202 | Volume Production | Digi-Key | WM1819-ND | 1.49 | 8.97
 | 76825-0008 | MOLEX 76825-0008. CONNECTOR, HEADER, 8POS, 2ROW, 5.7MM | CN20 | 1 | Molex | 76825-0008 | Volume Production | Digi-Key | WM11972-ND | 2.86 | 2.86
 | Header, Female, 2x2, RIght Angle, Pitch: 0.118" (3.00mm), THT | Connector Header Through Hole, Right Angle 4 position 0.118" (3.00mm) | CN21, CN23, CN27 | 3 | Molex | 0430450402 | Volume Production | Digi-Key | WM1820-ND | 2.26 | 6.79
 | LT Q39G-Q1OO-25-1 | LED GREEN DIFFUSED 0603 SMD | D1, D2, D4, D5, D6, D7, D11, D12, D13, D14 | 10 | Osram Opto | LT Q39G-Q1OO-25-1 | Volume Production | Digi-Key | 475-3442-1-ND | 0.2767 | 2.77
 | LED, 0805 (2012), Orange, Clear | LED, 0805 (2012), Orange, Clear | D3 | 1
17 | RB060M-60TR | Diode, Schottky, 60V, 2A | D8 | 1 | Rohm | RB060M-60TR | Volume Production | Digi-Key | 846-RB060M-60CT-ND | 0.43423 | 0.43423
 | DSS14UTR | Diode, Schottky, 40V, 1A | D9, D10 | 2 | Sangdest Microelectronics | DSS14UTR |  | Digi-Key | 1655-1927-1-ND | 0.15148 | 0.30295
 | LBQ39E-N1OO-35-1 | LED BLUE DIFFUSED 0603 SMD | D15 | 1 | Osram Opto | LBQ39E-N1OO-35-1 | Volume Production | Digi-Key | 475-2815-1-ND | 0.45443 | 0.45443
 | LSQ976-NR-1 | LED Red 645nm 2-Pin Chip 0603(1608Metric) T/R | D16 | 1 | Osram Opto | LSQ976-NR-1 | Volume Production | Digi-Key | 475-2512-1-ND | 0.28276 | 0.28276
 | CUS08F30,H3F | Diode Schottky 30V 800mA Surface Mount USC | D17, D18, D19 | 3 | Toshiba | CUS08F30,H3F | Volume Production | Digi-Key | CUS08F30H3FCT-ND | 0.32315 | 0.96945
 | PESD36VS2UT,215 | TVS DIODE 36V 60V SOT23 | D21, D22 | 2 | Nexperia | PESD36VS2UT,215 |  | Digi-Key | 1727-5397-1-ND | 0.39384 | 0.78768
 | SMD Fuse, 250mA, 63V, 1206 | SMD Fuse, 250mA, 63V, 1206 | F1 | 1 | Bel | C1Q250 | Volume Production | Digi-Key | 507-1073-1-ND | 0.31305 | 0.31305
 | BLM18AG601SN1D | Chip Ferrite Bead for General Use, 600 Ohm, 500 mA, -55 to 125 degC, 1.6 x 0.8 x 0.95 mm SMD, Tape and Reel | FB1 | 1 | Murata | BLM18AG601SN1D | Volume Production | Digi-Key | 490-1014-1-ND | 0.10098 | 0.10098
 | 1x2 Male Header |  | JP1, JP2, JP3, JP4 | 4 | Harwin | M20-9730246 | Volume Production | Digi-Key | 952-3073-ND | 0.11108 | 0.44433
 | SRP1270-2R2M | BOURNS SRP1270-2R2M Surface Mount Power Inductor, SRP1270 Series, 2.2 H, 22 A, 40 A, Shielded, 4200 ohm | L1 | 1 | Bourns | SRP1270-2R2M | Volume Production | Digi-Key | SRP1270-2R2MCT-ND | 1.69 | 1.69
 | PG0936.682NL | Inductor Power Shielded Wirewound 6.8uH/5.4uH 20% 100KHz Ferrite 18A 0.0035Ohm DCR Automotive | L2 | 1 | Pulse | PG0936.682NL | Volume Production | Digi-Key | 553-3159-ND | 3.27 | 3.27
 | 7447709150 | WURTH ELEKTRONIK - 7447709150 - Power Inductor (SMD), 15 µH, 6.5 A, Shielded, 8 A, WE-PD Series, 12mm x 12mm x 10mm | L3 | 1 | Wurth Electronics | 7447709150 | Volume Production | Digi-Key | 732-1242-1-ND | 2.43 | 2.43
16 | NR4018T6R8M | 6.8uH 1.06A | L4 | 1 | Taiyo Yuden | LMNR4018T6R8M |  | Digi-Key | 587-2657-1-ND | 0.41404 | 0.41404
 | Mount_Hole_3mm | Mounting hold for M3 hex standoff | MH1, MH2, MH3, MH4, MH5, MH6 | 6
 | MOSFET N-Channel, 40V, 100A, 272W | MOSFET N-Channel, 40V, 100A, 272W, Enh-Mode | Q1, Q2, Q7, Q8 | 4 | Nexperia | PSMN1R8-40YLC,115 |  | Digi-Key | 1727-1052-1-ND | 1.33 | 5.33
 | IPC50N04S5L5R5ATMA1 | N-CHANNEL_30/40V | Q3, Q4, Q5, Q6 | 4 | Infineon | IPC50N04S5L5R5ATMA1 |  | Digi-Key | IPC50N04S5L5R5ATMA1CT-ND | 0.86846 | 3.47
 | BC856A,215 | PNP 65V 100mA 250mW | Q10 | 1
 | BC846B,215 | NPN 65V 100mA 250mW | Q11, Q12, Q13, Q14, Q15 | 5
 | CRCW06036K34FKEA | VISHAY CRCW06036K34FKEA. SMD Chip Resistor, Thick Film, 6.34 kohm, 75 V, 0603 [1608 Metric], 100 mW, 1%, CRCW Series | R2, R3, R75, R86 | 4
 | ERJ3EKF10R0V | PANASONIC - ERJ3EKF10R0V - SMD Chip Resistor, 0603 [1608 Metric], 10 ohm, ERJ3EK Series, 75 V, Thick Film, 100 mW | R4, R5, R15, R16, R17, R18, R49, R50, R60, R61, R69, R70, R76, R77 | 14
 | HCS2512FTL300 | 300 µOhms ±1% 3W Chip Resistor 2512 (6432 Metric) Automotive AEC-Q200, Current Sense, Moisture Resistant Metal Element | R6, R7, R8, R74 | 4 | Stackpole Electronics | HCS2512FTL300 | Volume Production | Digi-Key | HCS2512FTL300CT-ND | 1.23 | 4.93
 | RC0603FR-0710KL | Res General Purpose Thick Film 0603 10K Ohm 1% 1/10W ±100ppm/°C Molded SMD Paper T/R | R9, R10, R11, R12, R13, R14, R30, R31, R32, R33, R34, R35, R36, R44, R52, R55, R63, R71, R94, R108, R113, R114, R115, R116, R117, R118, R119, R120, R121, R122 | 30
 | ERJ-3EKF5231V | GLOVE, POLYAMIDE, L/FREE, PU, SIZE 6 - More Details | R19, R37 | 2
 | ERJ-3EKF2102V | RESISTOR, 0603, 21K 1%, 0.1W | R20, R38 | 2
 | ERJ3EKF3652V | PANASONIC - ERJ3EKF3652V - SMD Chip Resistor, 0603 [1608 Metric], 36.5 kohm, ERJ3EK Series, 75 V, Thick Film, 100 mW | R21, R39 | 2
 | ERJ-3EKF5232V | ICK FILM, RESISTOR, 52.3KOHM, 100mW, ±1%; Product Range:PANASONIC - ERJ Series; Resistance:52.3kohm; Power Rating:100mW; Resistance Tolerance:± 1%; Resistor Case Style:0603 ^1608 Metric]; Resistor Element Type:Thick Film; MSL:- | R22, R40 | 2
 | ERJ-3EKF6652V | SISTOR, THICK FILM, 66.5KOHM, 100mW,1%; Product Range:PANASONIC - ERJ Series; Resistance:66.5kohm; Power Rating:100mW; Resistance Tolerance:± 1%; Resistor Case Style:0603 ^1608 Metric]; Resistor Element Type:Thick Film; MSL:- | R23, R41 | 2
 | ERJ-3EKF8252V | RES SMD 82.5K OHM 1% 1/10W 0603 | R24, R42 | 2
 | 20.5 Ohm, 1%, 1/10W , 0603, SMD | 20.5 Ohm, 1%, 1/10W , 0603, SMD | R25, R26, R78, R79 | 4 | Panasonic | ERJ3EKF20R5V | Volume Production | Digi-Key | P20.5HCT-ND | 0.03433 | 0.34335
 | 715R, 1%, 1/10W, 0603, SMD | 715R, 1%, 1/10W, 0603, SMD | R27 | 1 | Vishay | CRCW0603715RFKEA | Volume Production | Digi-Key | 541-715HCT-ND | 0.10098 | 0.10098
 | ERJ-3EKF5360V | SMD Chip Resistor, 0603 [1608 Metric], 536 ohm, ERJ3EK Series, 75 V, Thick Film, 100 mW | R43, R84 | 2
 | CSR1206-0R002F1 | RES 0.002 OHM 1W 1% 1206 | R45, R56, R67 | 3 | Riedon | CSR1206-0R002F1 | Volume Production | Digi-Key | 696-1370-1-ND | 0.59581 | 1.79
 | CRCW060344K2FKEA | Res Thick Film 0603 44.2K Ohm 1% 0.1W(1/10W) ±100ppm/C Pad SMD Automotive T/R | R46 | 1
 | CRCW06031K30FKEA | Res Thick Film 0603 1.3K Ohm 1% 1/10W 100ppm/C Molded SMD SMD Paper T/R | R47, R58 | 2
 | CRCW06035M49FKEA | RES SMD 5.49M OHM 1% 1/10W 0603 | R48 | 1 | Vishay | CRCW06035M49FKEA | Volume Production | Digi-Key | 541-5.49MHCT-ND | 0.10098 | 0.10098
 | ERJ-3EKF7322V | Res Thick Film 0603 73.2K Ohm 1% 0.1W(1/10W) ±100ppm/C Pad SMD Automotive T/R | R51 | 1
 | RC0603FR-072K26L | RES SMD 2.26K OHM 1% 1/10W 0603 | R54, R95, R96 | 3
 | ERJ-3EKF4123V | GLOVE, POLYAMIDE, L/FREE, PU, SIZE 6 - More Details | R57 | 1
 | CRCW06039M76FKEA | RES SMD 9.76M OHM 1% 1/10W 0603 | R59 | 1
 | ERJ-3EKF1913V | RES, THICK FILM, 191KOHM, 0.1W, 0603 | R62 | 1
 | ERJ-3EKF3321V | RES SMD 3.32K OHM 1% 1/10W 0603 | R66 | 1
 | CRCW0603-100KFKEA | Resistor; Thick Film; 100 Kilohms; 0.1 W; 1%; SMT; 0603; TCR 37 ppm/DegC; Tape and Reel | R68, R102, R107, R109, R110, R111, R112 | 7
 | RC0603FR-076K65L | RES SMD 6.65K OHM 1% 1/10W 0603 | R72 | 1
8 | 10kR, 1%, 1/10W, 0603 SMD | 10kR, 1%, 1/10W, 0603 SMD | R80, R87, R89, R91, R92, R97, R98 | 7 | Yageo Phycomp | RC0603FR-0710KL | Volume Production | Digi-Key | 311-10.0KHRDKR-ND | 0.02222 | 0.22217
7 | 3.9k, 5%, 1/8W, 0805 SMD | 3.9k, 5%, 1/8W, 0805 SMD | R82 | 1 | Stackpole Electronics | RMCF0805JT3K90 | Volume Production | Digi-Key | RMCF0805JT3K90DKR-ND | 0.10098 | 0.10098
10 | 680, 5%, 1/8W, 0805 SMD | 680, 5%, 1/8W, 0805 SMD | R83 | 1 | Stackpole Electronics | RMCF0805JT680R | Volume Production | Digi-Key | RMCF0805JT680RDKR-ND | 0.10098 | 0.10098
 | RC0603FR-07110RL | RES SMD 110 OHM 1% 1/10W 0603 | R85, R88, R90 | 3
 | CRCW0603330RFKEA | Res Thick Film 0603 330 Ohm 1% 0.1W(1/10W) +/-100ppm/ßC Pad SMD Automotive T/R | R93 | 1
 | RC0603FR-0733RL | Res Thick Film 0603 33 Ohm 1% 1/10W +/-100ppm/ßC Molded SMD Paper T/R | R99, R101 | 2
 | RC0603FR-07120RL | Res Thick Film 0603 120 Ohm 1% 0.1W(1/10W) ±100ppm/C Epoxy SMD T/R | R100 | 1
 | ERJ3EKF1001V | Res Thick Film 0603 1K Ohm 1% 1/10W ±100ppm/°C Molded SMD Punched Carrier T/R | R104 | 1
 | PTS645SL43SMTR92LFS | Black Switch Tactile N.O. SPST Round Button Gull Wing 0.05A 12VDC 100000Cycles 1.27N SMD T/R | SW1 | 1 | ITT C&K | PTS645SL43SMTR92LFS | Volume Production | Digi-Key | CKN10880CT-ND | 0.31305 | 0.31305
 | DPDT, 12V, 200mA, SMT | DPDT, 12V, 200mA, SMT | SW2 | 1 | Nidec Copal | CL-SB-22A-01T | Volume Production | Digi-Key | 563-1338-1-ND | 1.08 | 1.08
 | INA226AIDGSR | Bi Directional Current and Power Monitor 10-Pin VSSOP T/R | U1, U2, U3, U6, U8, U10, U11 | 7 | Texas Instruments | INA226AIDGSR | Volume Production | Digi-Key | 296-29034-1-ND | 3.21 | 22.48
 | MIC5014YM-TR | High-Side or Low-Side Gate Driver IC Non-Inverting 8-SOIC | U4, U12 | 2 | Microchip | MIC5014YM-TR | Volume Production | Digi-Key | 576-1233-1-ND | 2.18 | 4.36
13 | LM3150MHX/NOPB | IC REG CTRLR BUCK 14TSSOP | U5, U7 | 2 | TI National Semiconductor | LM3150MHX/NOPB | Volume Production | Digi-Key | 296-35276-1-ND | 3.18 | 6.36
 | BD9E302EFJ-E2 | IC REG BUCK ADJ 3A 8HTSOP-J | U9 | 1
11 | BD9G101G-TR | DC-DC Regulator, 6V-42V in, 1V-29.4V out, 500mA | U13 | 1 | Rohm | BD9G101G-TR | Volume Production | Digi-Key | BD9G101G-CT-ND | 1.5 | 1.5
1 | 3.3V 250mA Linear Reg LDO | IC REG LINEAR 3.3V 250MA SOT23-3 | U14 | 1 | Diodes | AP2138N-3.3TRG1 | Volume Production | Digi-Key | AP2138N-3.3TRG1DICT-ND | 0.48472 | 0.48472
 | STM32F413RGT6 | STMICROELECTRONICS - STM32F413RGT6 - MCU, ARM CORTEX-M4, 100MHZ, LQFP-64 | U15 | 1
 | CD74HC194PWR | IC SHFT REGSTR UNIV BIDIR16TSSOP | U16 | 1 | Texas Instruments | CD74HC194PWR | Volume Production | Digi-Key | 296-12794-1-ND | 0.60591 | 0.60591
 | CAN Transceiver | 1/1 Transceiver Half CANbus 8-SO | U17 | 1 | NXP Semiconductors | TJA1042T/3,118 | Volume Production | Digi-Key | 568-8678-1-ND | 1.32 | 1.32
 | MS560702BA03-50 Pressure Sensor | 1kPa to 120 kPa | U18 | 1
 | Si700XX | I2C Humidity and Temperature Sensor | U19 | 1 | Silicon Labs | SI7021-A20-GM | Volume Production | Digi-Key | 336-3140-5-ND | 3.09 | 3.09
 | ST3232CDR | Dual Transmitter/Receiver RS-232 16-Pin SO T/R | U20 | 1 | STMicroelectronics | ST3232CDR | Volume Production | Digi-Key | 497-3731-1-ND | 1.12 | 1.12
 | Oscillator 8MHz 40ESR | 8Mhz 40ESR 16pF -20°C ~ 70°C | X1 | 1 | Diodes | GC0800044 | Volume Production | Digi-Key | GC0800044CT-ND | 0.60591 | 0.60591
 | 3555-2 | FUSE HOLDER MAXI AUTO BLADE PC | XF1, XF2, XF6 | 3 | Keystone Electronics | 3555-2 | Volume Production | Digi-Key | 36-3555-2-ND | 1.72 | 5.15
 | 3557-2 | Fuse Holder; Auto; 2 in1 Blade; THM; 1 Fuse; Vertical; 30 Amps | XF3, XF4, XF5 | 3

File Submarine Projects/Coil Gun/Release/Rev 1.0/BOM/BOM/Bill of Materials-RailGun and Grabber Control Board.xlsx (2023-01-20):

Line # | Name | Description | Designator | Revision ID | Quantity | Manufacturer 1 | Manufacturer Part Number 1 | Manufacturer Lifecycle 1 | Supplier 1 | Supplier Part Number 1 | Supplier Unit Price 1 | Supplier Subtotal 1
 | CL10B104JB8NNNC | CAP CER 0.1UF 50V X7R 0603 | C1, C3, C8, C11, C14, C15, C16, C17, C18, C19 | CMP-00000-3 | 10 | Samsung | CL10B104JB8NNNC | Volume Production
 | CL21B105KBFNNNG | SAMSUNG ELECTRO-MECHANICS - CL21B105KBFNNNG - MLCC CAPACITORS | C2, C12 | CMP-00005-1 | 2 | Samsung | CL21B105KBFNNNG | Volume Production
 | 1uF 50V 0603 SMD, Ceramic | Capacitor, Ceramic, 50V, +/- 10%, 0603 SMD, X5R | C4_Gin1, C4_Gin2, C4_Gin3, C21, C22 | CMP-006-0028-1 | 5 | Samsung | CL10A105KB8NNNC | Volume Production
 | 0.1uF, 50V, 10%, X7R, 1608 | CAP CER 0.1UF 50V 10% X7R 1608 (0603) | C5_Gin1, C5_Gin2, C5_Gin3, C6_Gin1, C6_Gin2, C6_Gin3, C?_Gin1, C?_Gin2, C?_Gin3 | CMP-006-0008-1 | 9 | Samsung | CL10B104KB8SFNC | Volume Production
 | 10uF 50V 1206 SMD, Ceramic | Capacitor, Ceramic, 50V, +/- 10%, 1206 SMD, X5R | C7_Gin1, C7_Gin2, C7_Gin3 | CMP-006-0018-1 | 3 | Samsung | CL31A106KBHNNNE | Volume Production
 | 16pF Ceramic 50V 5% 0603 | Cap Ceramic 16pF 50V C0G 5% SMD 0603 125C Paper T/R | C9, C10 | CMP-00087-2 | 2 | Murata | GRM1885C1H160JA01D | Volume Production
 | 2.2uF, 50V, 0603 SMD, X5R, Ceramic | Capacitor, Ceramic, 50V, 10%, 0603 SMD, X5R | C13 | CMP-006-0030-1 | 1 | Murata | GRM188R61H225KE11D | Volume Production
 | CL31B106KBHNNNE | Cap Ceramic 10uF 50V X7R 10% Pad SMD 1206 125°C T/R | C20 | CMP-00004-1 | 1 | Samsung | CL31B106KBHNNNE | New Product
 | 1x2 Shrouded Right Angle | 02 MTE HDR SRRA LATCH | CN1 | CMP-00010-3 | 1 | TE Connectivity | 5-104935-5 | Volume Production
 | Header, Female, 2x2, RIght Angle, Pitch: 0.118" (3.00mm), THT | Connector Header Through Hole, Right Angle 4 position 0.118" (3.00mm) | CN2_Gin1, CN2_Gin2, CN2_Gin3 | CMP-005-0021-4 | 3 | Molex | 0430450402 | Volume Production
 | ST Debug Header 10-pin THT | CONN HEADER VERT 10POS 2.54MM | CN3 | CMP-00011-6 | 1 | Sullins | SBH11-PBPC-D05-ST-BK | Volume Production
 | Header, Male, 1x4, RA, Pitch 0.1" (2.54mm) | Connector Header Through Hole, Right Angle 4 position 0.100" (2.54mm) | CN4, CN5 | CMP-005-0029-3 | 2 | TE Connectivity | 5-104935-1 | Volume Production
 | 76825-0006 | CONNECTOR, HEADER, 6POS, 2ROW, 5.7MM; Product Range:Mega-Fit 76825 Series; Contact Termination Type:Through Hole; Gender:Header; No. of Contacts:6; Pitch Spacing:5.7mm; Contact Plating:Tin Plated Contacts; Contact Material:Copper | CN6 | CMP-00049-2 | 1 | Molex | 76825-0006 | Volume Production
 | TSSA5U50E3GCT-ND | Diode Schottky 50V 5A Surface Mount DO-214AC (SMA) | D1_Gin1, D1_Gin2, D1_Gin3 | CMP-057-0021-1 | 3 | Taiwan Semiconductor | TSSA5U50 E3G | Unknown
 | LSQ976-NR-1 | LED Red 645nm 2-Pin Chip 0603(1608Metric) T/R | D2 | CMP-00066-2 | 1 | Osram Opto | LSQ976-NR-1 | Volume Production
 | LBQ39E-N1OO-35-1 | LED BLUE DIFFUSED 0603 SMD | D3 | CMP-00063-3 | 1 | Osram Opto | LBQ39E-N1OO-35-1 | Volume Production
 | LT Q39G-Q1OO-25-1 | LED GREEN DIFFUSED 0603 SMD | D4, D6, D7, D8 | CMP-00064-3 | 4 | Osram Opto | LT Q39G-Q1OO-25-1 | Volume Production
 | CUS08F30,H3F | Diode Schottky 30V 800mA Surface Mount USC | D5 | CMP-057-0000-2 | 1 | Toshiba | CUS08F30,H3F | Volume Production
 | SMD Fuse, 2A, 63V, | SMD Fuse, 2A, 63V, | F? | CMP-027-0004-1 | 1 | Bel TRP | C1F2 | Volume Production
 | BLM18AG601SN1D | MURATA - BLM18AG601SN1D - Feritový Korálek, 0603 / 1608, 600 ohm, 500 mA, Série BLM18A, 0.38 ohm, ± 25% | FB1 | CMP-00016-1 | 1 | Murata | BLM18AG601SN1D | Volume Production
 | 1x2 Male Header |  | JP1, JP2, JP3 | CMP-004-0001-1 | 3 | Harwin | M20-9730246 | Volume Production
 | Mount_Hole_3mm | Mounting hold for M3 hex standoff | MH1, MH2, MH3, MH4 | CMP-004-0010-4 | 4
 | MOSFET N-Channel, 40V, 100A, 272W | MOSFET N-Channel, 40V, 100A, 272W, Enh-Mode | Q1_Gin1, Q1_Gin2, Q1_Gin3 | CMP-052-0019-1 | 3 | Nexperia | PSMN1R8-40YLC,115 | Unknown
 | RC0603FR-0733RL | Res Thick Film 0603 33 Ohm 1% 1/10W +/-100ppm/ßC Molded SMD Paper T/R | R1, R3 | CMP-00060-1 | 2 | Yageo | RC0603FR-0733RL | Volume Production
 | RC0603FR-07120RL | Res Thick Film 0603 120 Ohm 1% 0.1W(1/10W) ±100ppm/C Epoxy SMD T/R | R2 | CMP-00061-1 | 1 | Yageo | RC0603FR-07120RL | Volume Production
 | 78.7kR, 1%, 1/10W, 0603 | Res Thick Film 0603 78.7K Ohm 1% 1/10W 100ppm/C Molded SMD SMD Paper T/R | R4_Gin1, R4_Gin2, R4_Gin3 | CMP-00095-1 | 3 | Stackpole Electronics | RMCF0603FT78K7 | Volume Production
 | 100kR, 1%, 1/10W, 0603 SMD | 100kR, 1%, 1/10W, 0603 SMD | R5_Gin1, R5_Gin2, R5_Gin3, R6_Gin1, R6_Gin2, R6_Gin3, R7_Gin1, R7_Gin2, R7_Gin3 | CMP-047-0010-1 | 9 | Yageo | RC0603JR-07100KL | Volume Production
 | 10kR, 1%, 1/10W, 0603 SMD | 10kR, 1%, 1/10W, 0603 SMD | R8_Gin1, R8_Gin2, R8_Gin3, R13, R14, R16, R17, R20, R23, R24, R25 | CMP-047-0013-1 | 11 | Yageo Phycomp | RC0603FR-0710KL | Volume Production
 | 0R005, 1%, 3W, 2512 SMD | 0R005, 1%, 3W, 2512 SMD | R9_Gin1, R9_Gin2, R9_Gin3 | CMP-047-0004-1 | 3 | Bourns | CRE2512-FZ-R005E-3 | Volume Production
 | CRCW0603330RFKEA | Res Thick Film 0603 330 Ohm 1% 0.1W(1/10W) +/-100ppm/ßC Pad SMD Automotive T/R | R10 | CMP-00067-2 | 1 | Vishay | CRCW0603330RFKEA | Volume Production
 | 1kR, 1%, 1/10W , 0603, SMD | 1kR, 1%, 1/10W , 0603, SMD | R11, R26, R27, R28 | CMP-047-0024-1 | 4 | Yageo | RC0603FR-071KL | Volume Production
 | RC0603FR-07110RL | RES SMD 110 OHM 1% 1/10W 0603 | R12, R15, R31 | CMP-00069-1 | 3 | Yageo | RC0603FR-07110RL | Volume Production
 | ERJ-3EKF8252V | RES SMD 82.5K OHM 1% 1/10W 0603 | R18 | CMP-00085-1 | 1 | Panasonic | ERJ-3EKF8252V | Volume Production
 | 16kR, 1%, 1/10W, 0603 SMD | 16kR, 1%, 1/10W, 0603 SMD | R19 | CMP-047-0021-1 | 1 | Yageo | RC0603FR-0716KL | Volume Production
 | RC0603FR-0710KL | Res General Purpose Thick Film 0603 10K Ohm 1% 1/10W ±100ppm/°C Molded SMD Paper T/R | R21 | CMP-00037-1 | 1 | Yageo | RC0603FR-0710KL | Volume Production
 | 27kR, 1%, 1/10W, 0603 | Res Thick Film 0603 27K Ohm 1% 0.1W(1/10W) ±100ppm/C Pad SMD Automotive T/R | R22 | CMP-00090-2 | 1 | TE Connectivity | CRGCQ0603F27K | Unknown
 | CRCW06036K34FKEA | VISHAY CRCW06036K34FKEA. SMD Chip Resistor, Thick Film, 6.34 kohm, 75 V, 0603 [1608 Metric], 100 mW, 1%, CRCW Series | R29 | CMP-00072-1 | 1 | Vishay | CRCW06036K34FKEA | Volume Production
 | ERJ-3EKF5360V | SMD Chip Resistor, 0603 [1608 Metric], 536 ohm, ERJ3EK Series, 75 V, Thick Film, 100 mW | R30 | CMP-00071-1 | 1 | Panasonic | ERJ-3EKF5360V | Volume Production
 | 0R02, 1%, 2W, 2512 SMD | 0R02, 1%, 2W, 2512 SMD | R?_Gin1, R?_Gin2, R?_Gin3 | CMP-047-0006-1 | 3 | TE Connectivity | RLP73V3AR020FTDF | Unknown
 | 80.6kR, 1%, 1/10W, 0603 | Res Thick Film 0603 80.6K Ohm 1% 0.1W(1/10W) ±100ppm/C Molded SMD Automotive Paper T/R | R?_Gin1, R?_Gin2, R?_Gin3 | CMP-00098-1 | 3 | Vishay | CRCW060380K6FKEA | Volume Production
 | PTS645SL43SMTR92LFS | Black Switch Tactile N.O. SPST Round Button Gull Wing 0.05A 12VDC 100000Cycles 1.27N SMD T/R | SW1 | CMP-00077-1 | 1 | ITT C&K | PTS645SL43SMTR92LFS | Volume Production
 | PESD36VS2UT,215 | TVS DIODE 36V 60V SOT23 | TVS1, TVS2 | CMP-058-0000-2 | 2 | Nexperia | PESD36VS2UT,215 | Unknown
 | CAN Transceiver | 1/1 Transceiver Half CANbus 8-SO | U1 | CMP-032-0000-2 | 1 | NXP Semiconductors | TJA1042T/3,118 | Volume Production
 | Op amp 1.8-6V rail-to-rail (SOT23-5) | Op amp 1.8-6V rail-to-rail (SOT23-5) | U2_Gin1, U2_Gin2, U2_Gin3 | CMP-042-0002-1 | 3 | Microchip | MCP6001T-I/OT | Volume Production
 | MIC5014YM-TR | High-Side or Low-Side Gate Driver IC Non-Inverting 8-SOIC | U3_Gin1, U3_Gin2, U3_Gin3 | CMP-028-0000-2 | 3 | Microchip | MIC5014YM-TR | Volume Production
 | STM32F413RGT6 | STMICROELECTRONICS - STM32F413RGT6 - MCU, ARM CORTEX-M4, 100MHZ, LQFP-64 | U4 | CMP-00006-1 | 1 | STMicroelectronics | STM32F413RGT6 | Unknown
 | STM32F413RGT6 | STMICROELECTRONICS - STM32F413RGT6 - MCU, ARM CORTEX-M4, 100MHZ, LQFP-64 | U5 | CMP-00006-2 | 1 | STMicroelectronics | STM32F413RGT6 | Unknown
 | 3.3V 250mA Linear Reg LDO | IC REG LINEAR 3.3V 250MA SOT23-3 | U6 | CMP-00003-1 | 1 | Diodes | AP2138N-3.3TRG1 | Volume Production | Digi-Key | AP2138N-3.3TRG1
 | INA168, Current Sensor, High-Side, Analog | INA168, Current Sensor, High-Side, Analog | U?_Gin1, U?_Gin2, U?_Gin3 | CMP-048-0001-1 | 3 | Texas Instruments | INA168NA/3K | Volume Production
 | CRYSTAL 8.0MHZ 16PF SMD | 8MHz ±30ppm Crystal 16pF 80 Ohms 4-SMD, No Lead | X1 | CMP-00079-2 | 1 | IQD | LFXTAL026380REEL | Volume Production

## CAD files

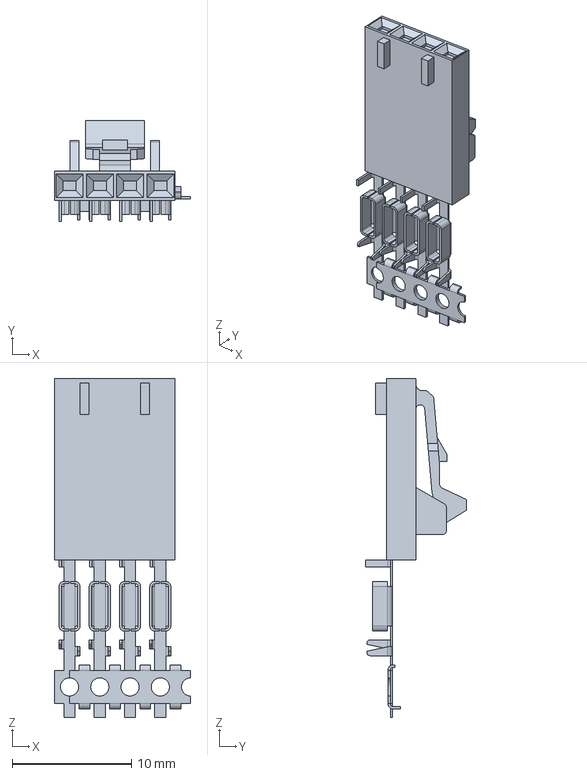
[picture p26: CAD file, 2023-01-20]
Submarine Projects/Power Board/Release/Rev 2.0/3D Model/Parts/c-0103961-53-k-3d.stp
11.4 x 8.48 x 28.4 mm

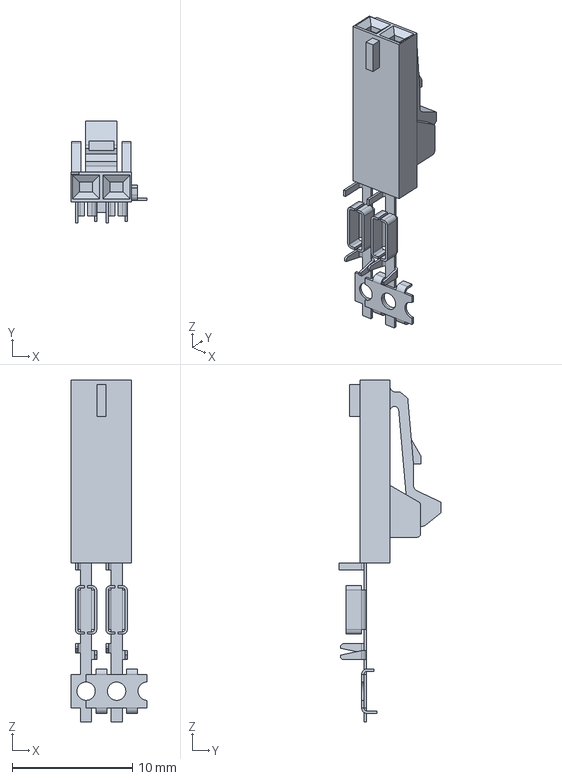
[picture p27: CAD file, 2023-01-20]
Submarine Projects/Power Board/Release/Rev 2.0/3D Model/Parts/c-5-103960-1-m-3d.stp
6.35 x 8.48 x 28.4 mm

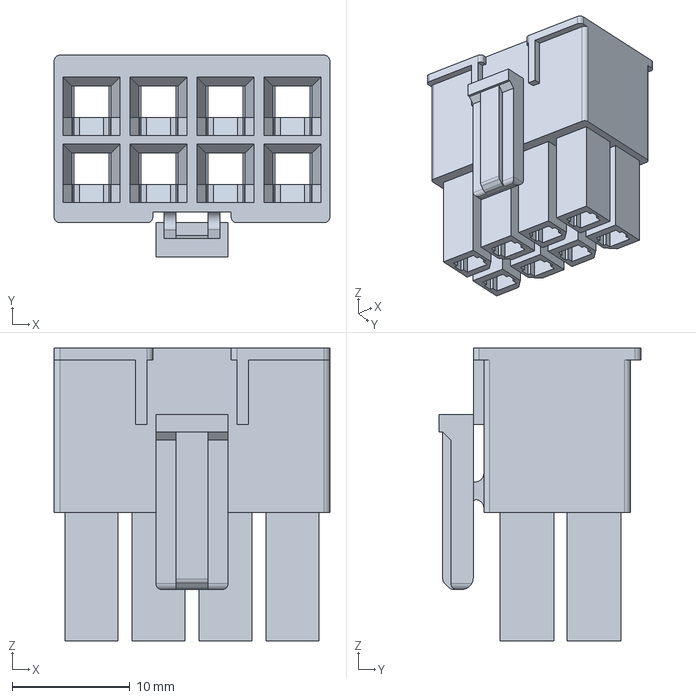
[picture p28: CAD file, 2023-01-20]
Submarine Projects/Power Board/Release/Rev 2.0/3D Model/Parts/1716920108.stp
23.4 x 17.2 x 24.9 mm

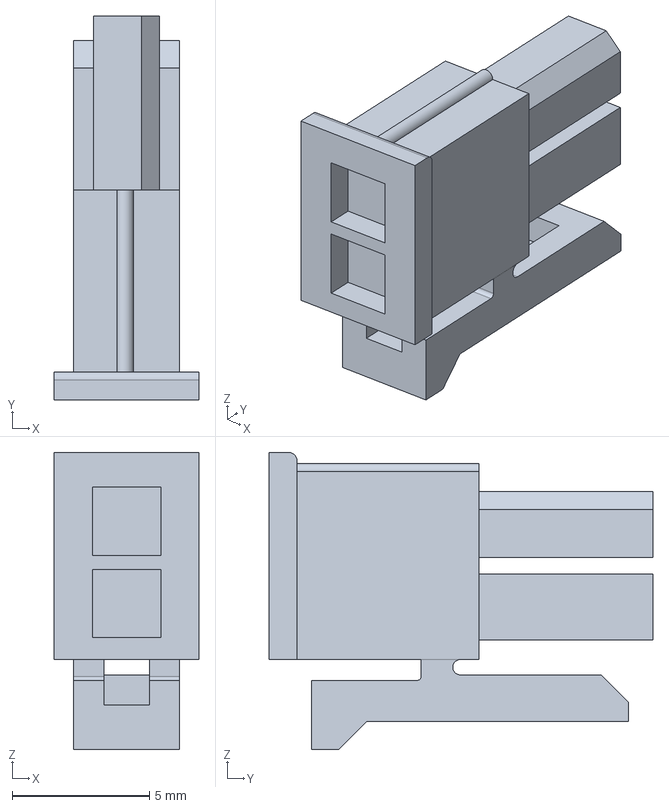
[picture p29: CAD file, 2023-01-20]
Submarine Projects/Power Board/Release/Rev 2.0/3D Model/Parts/430250200.stp
5.28 x 14.0 x 10.8 mm

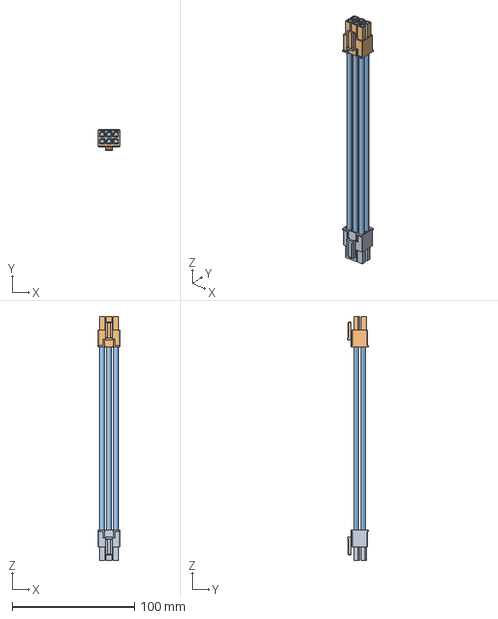
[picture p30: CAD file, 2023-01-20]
Submarine Projects/Power Board/Release/Rev 2.0/3D Model/Parts/451360601.stp
17.8 x 17.2 x 199.8 mm

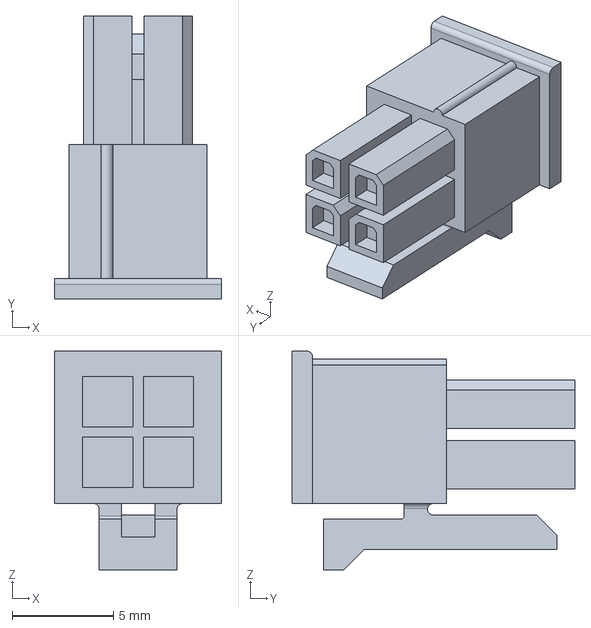
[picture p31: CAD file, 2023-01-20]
Submarine Projects/Power Board/Release/Rev 2.0/3D Model/Parts/430250400.stp
8.27 x 14.0 x 10.8 mm

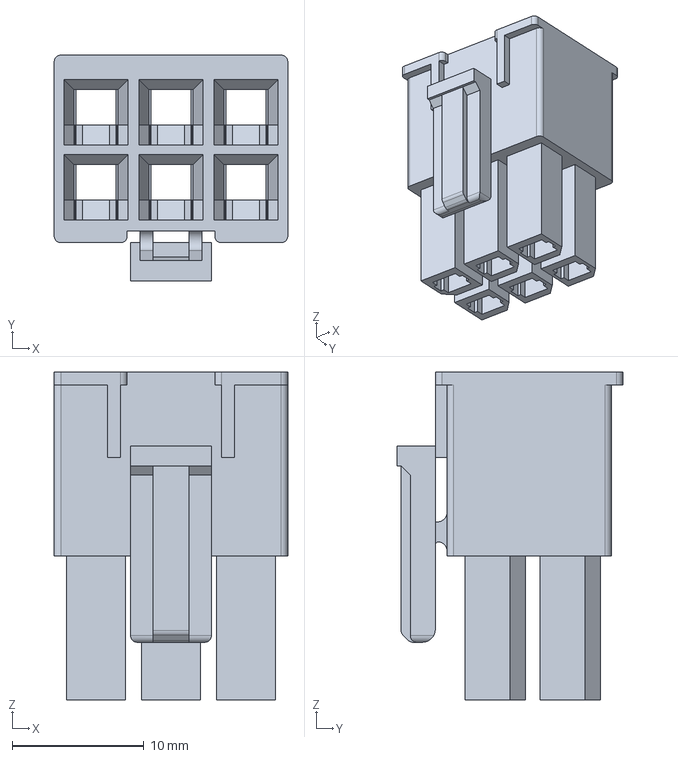
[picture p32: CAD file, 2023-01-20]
Submarine Projects/Power Board/Release/Rev 2.0/3D Model/Parts/1700010106.stp
17.8 x 17.2 x 24.9 mm

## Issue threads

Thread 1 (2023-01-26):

IMU Troubleshooting

anijjar, 2023-01-26:
The software team reports a few issues with the new IMU board

- [ ] The board sometimes doesn't get recognized by the jetson
- [ ] The 3d model slowly rotates while the sensor is stationary.

Further investigation is required.

anijjar, 2023-01-27:
After speaking with Rob, he said that the sensor may need to be calibrated. I will reach out to the contact after getting their information.

I printed out the Ros topic and saw that the y and x directions were slowly incrementing. Lets get it calibrated and see if the problem persists

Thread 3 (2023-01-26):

Testing ESC Board

anijjar, 2023-01-26:
I saw a few of Poorna's ESC boards around the club room. It would good to see if that design works well and if it does, use it in a future motor controller revision or as a standalone device.

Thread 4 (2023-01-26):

Get Board Dimensions for the Mechanical Team

anijjar, 2023-01-26:
The mech team needs to get the board dims for all the PCBs going inside the main enclosure.

anijjar, 2023-01-30:
| Device| X Dim | Y Dim
| ----------- | ----------- | ----------- |
| Power Board | 6295mil |3940mil |
| Motor Controller  | 6100mil  | 4400mil |
| IMU 2  | 2920mil  | 1970mil|
| IMU 1 | | |
| Jetson | 170mm| 170mm|
| Hydrophone | 4846.930mil  | 2730mil|
| Ball Dropper| TBD| TBD|
| Coil Gun | TBD | TBD|
| Grabber Arm | TBD| TBD |
| LCD Diagnostics | 96.52mm  |66.04mm |

Closed 2023-01-30.

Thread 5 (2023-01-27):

Hydrophone reassembly

anijjar, 2023-01-27:
The hydrophone has been dissasembled. We need someone to connect the preamp board to the sensors and check if they work. Moreover, we need to look into where the control board is and if it works good. We need a device that can emit pings, so I recommend we look into getting a pinger from blue robotics.

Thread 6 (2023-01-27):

Soldering Motor Controller V3

anijjar, 2023-01-27:
Rob is soldering one board, but it would be nice to have a second one for development purposes

Closed 2023-05-04.

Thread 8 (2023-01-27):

Poorna's ESC Controller

anijjar, 2023-01-27:
We have a bunch of ESC controllers designed back in 2020. It would be nice if someone soldered one up and tested to see if it works correctly

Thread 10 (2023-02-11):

Soldering Hydrophone Control Board

anijjar, 2023-02-11:

anijjar, 2023-05-04:
This board will not work because the traces connecting the microcontroller and the Pre-amp circuit are crossing a split in the ground plane. This will greatly reduce the integrity of the signal. Since competition is coming up, we don't have time to fix this problem

Closed 2023-05-04.

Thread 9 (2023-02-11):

IMU Breakout Board redesign

anijjar, 2023-02-11:
Fumika is working on a new revision. She is swapping out a header and rerouting.

anijjar, 2023-04-05:
Fumika is working on this. Adding a Uart to USB to converter to it so we can communicate it Via COM port. This is on schedule to be ordered friday

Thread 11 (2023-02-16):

Updating the component library to a standard naming convention

anijjar, 2023-02-16:
The components all have different naming conventions. Someone should go in and rename them to follow somewhat predictable scheme. Such as for headers

Header, <male or female>, <number of pins>, <pitch in mm> <special features>
Header, Male, 1x7, 2.54mm RA

This will be an ongoing issue

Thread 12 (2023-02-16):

Design Spec: Power Board V4

anijjar, 2023-02-16:
Issue to track discussion on the next revision of the power board.

- Add active current limiting via PWM and Opamps. Useful so we aren't arbitrarily dumping current into the motor controller and torpedo launcher
- ...

anijjar, 2023-05-04:
Add a water sensor, Pressure Sensor, IMU sensor

anijjar, 2023-05-04:
Simple Battery Bridge Circuit

anijjar, 2023-05-04:
Automotive Fuse from Raw battery input to rest of circuit

anijjar, 2023-05-04:
CAN bus, UART, and SPI communications over a single connector. Use a transistor to switch between communication lines

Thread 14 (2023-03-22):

Alice's First Project: ICM-20602 Breakout board

anijjar, 2023-03-22:
The ICM-20602 is a IMU IC that is really cheap. Alice completed the initial design and she is ready to get it built.

**Tasks:**
- [x] Do a design review and make notes on improvements here.
- [x] Generate an output job file to create the gerber files.

anijjar, 2023-04-05:
Alice said there are no DRVs. Her board is ready to be ordered

anijjar, 2023-04-08:
Generated Gerber Files and Placed the order alongside the IMU sensor, ESC prototype and a second layout

anijjar, 2023-05-04:
Board has been ordered and in transit

Closed 2023-05-04.

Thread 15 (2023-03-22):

Design Coil Gun Replacement

anijjar, 2023-03-22:
Karan wants a coil gun board that uses a capacitor bank rather than a dead short from the main power supply. This board will need a CAN bus connection for production and also a USB Connector for easy programming. Use a mosfet switch to switch the capacitor charge circuit to the launch circuit.

The charging circuit will be an RC network, so the time constant is RC. Meaning the capacitors will fully charge 5*RC. Design accordingly.

Once the caps switch, the charge stored in the electric field will be dumped into a solenoid (with a flyback diode to dissipate energy) to launch the projectile. The force induced by the inductor is directly proportional to the number of turns of the wire and the current being sinked.

An important note is that adding a series resistance to the launch circuit will reduce the amount of current dumped greatly, but it will remove any-sort of oscillations. Oscillations are a problem because the direction of the current will flip, causing the projectile to lose force. 1 ohm power resistor should be fine, but this doesnt need to be included in the schematic.

Use screw-in connectors for the solenoid connection.

Keep your power traces thick and untented (exposed)

anijjar, 2023-04-05:
Board designed, reviewed and ready to be ordered.

I should show the circuit to Jens once and get roasted. Before the order on thursday

anijjar, 2023-05-04:
Rather than using electrolytic caps, which would require high voltage, I went with super capacitors because they can store much greater charge at lower voltages. Robosub has a 55V potential limit before we need to get permission, so this solution is better. The supercaps provide more energy than Karans prototype so I predict that the projectile will launch with a greater force.

Closed 2023-05-04.

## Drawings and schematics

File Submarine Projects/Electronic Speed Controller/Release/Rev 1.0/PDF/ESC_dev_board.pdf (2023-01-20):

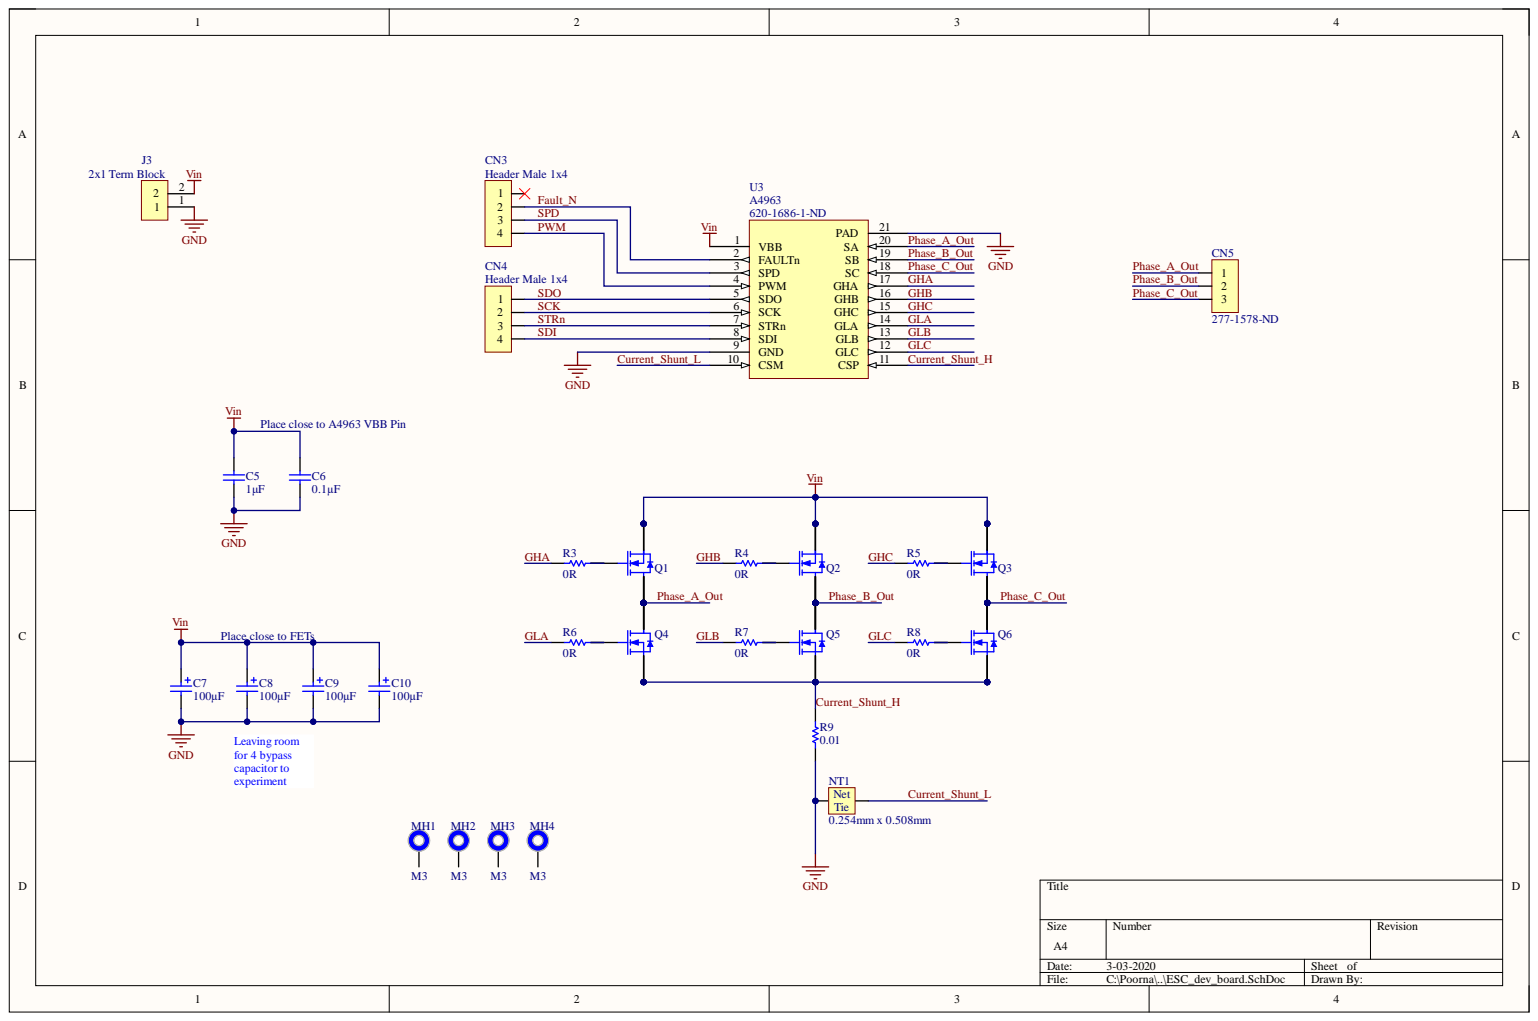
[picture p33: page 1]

PWM 4 | GHA

1 2 3 4 | SDO | SDO 5 | GHB

SCK | SCK 6 | GHC

Place close to A4963 VBB Pin

Place close to FETs

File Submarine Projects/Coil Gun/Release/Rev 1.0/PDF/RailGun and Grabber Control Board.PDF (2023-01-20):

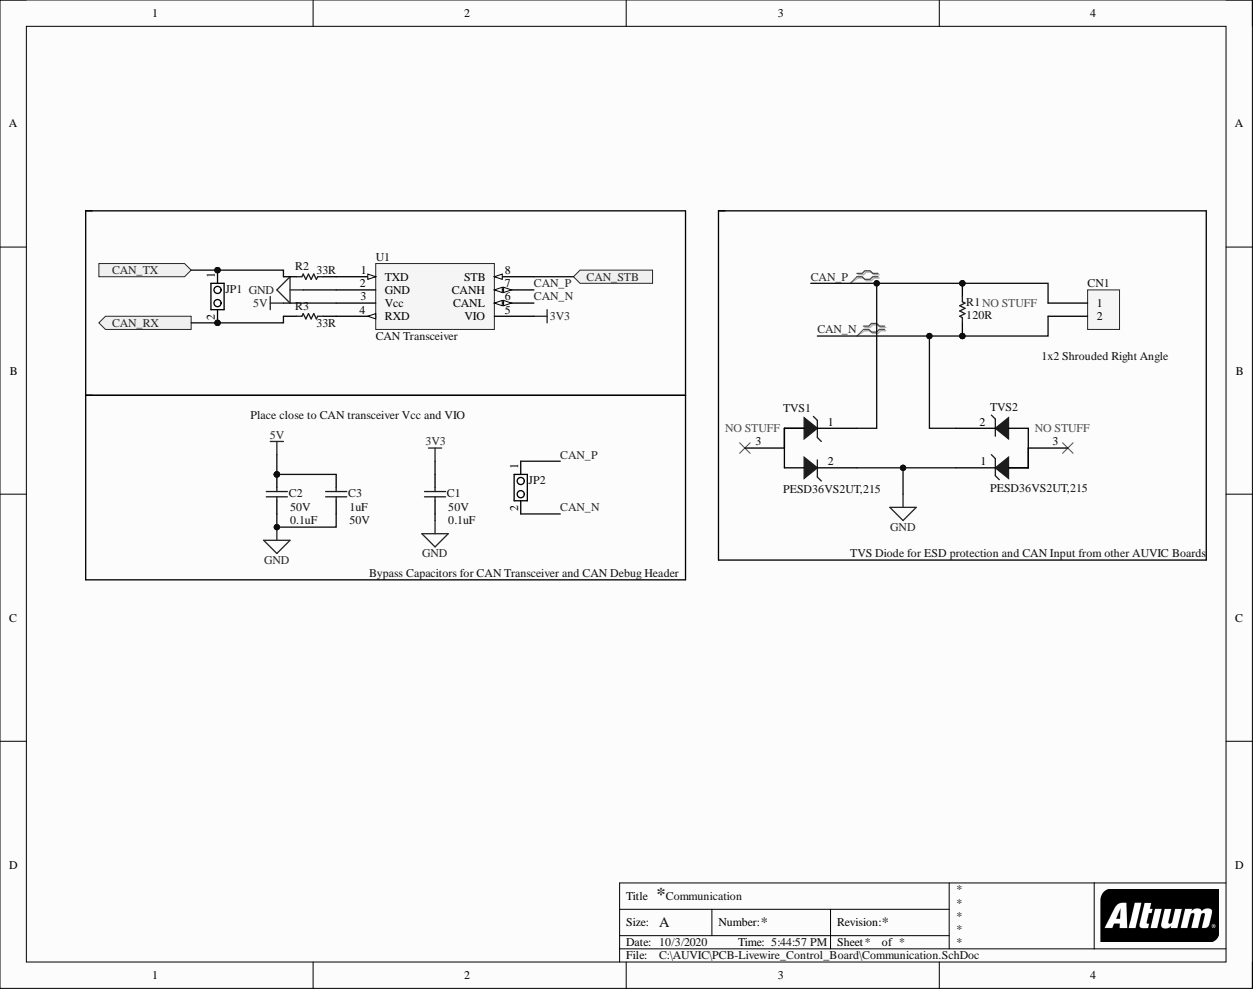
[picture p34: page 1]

Place close to CAN transceiver Vcc and VIO

TVS Diode for ESD protection and CAN Input from other AUVIC Boards

Bypass Capacitors for CAN Transceiver and CAN Debug Header

C:\AUVIC\PCB-Livewire_Control_Board\Communication.SchDoc

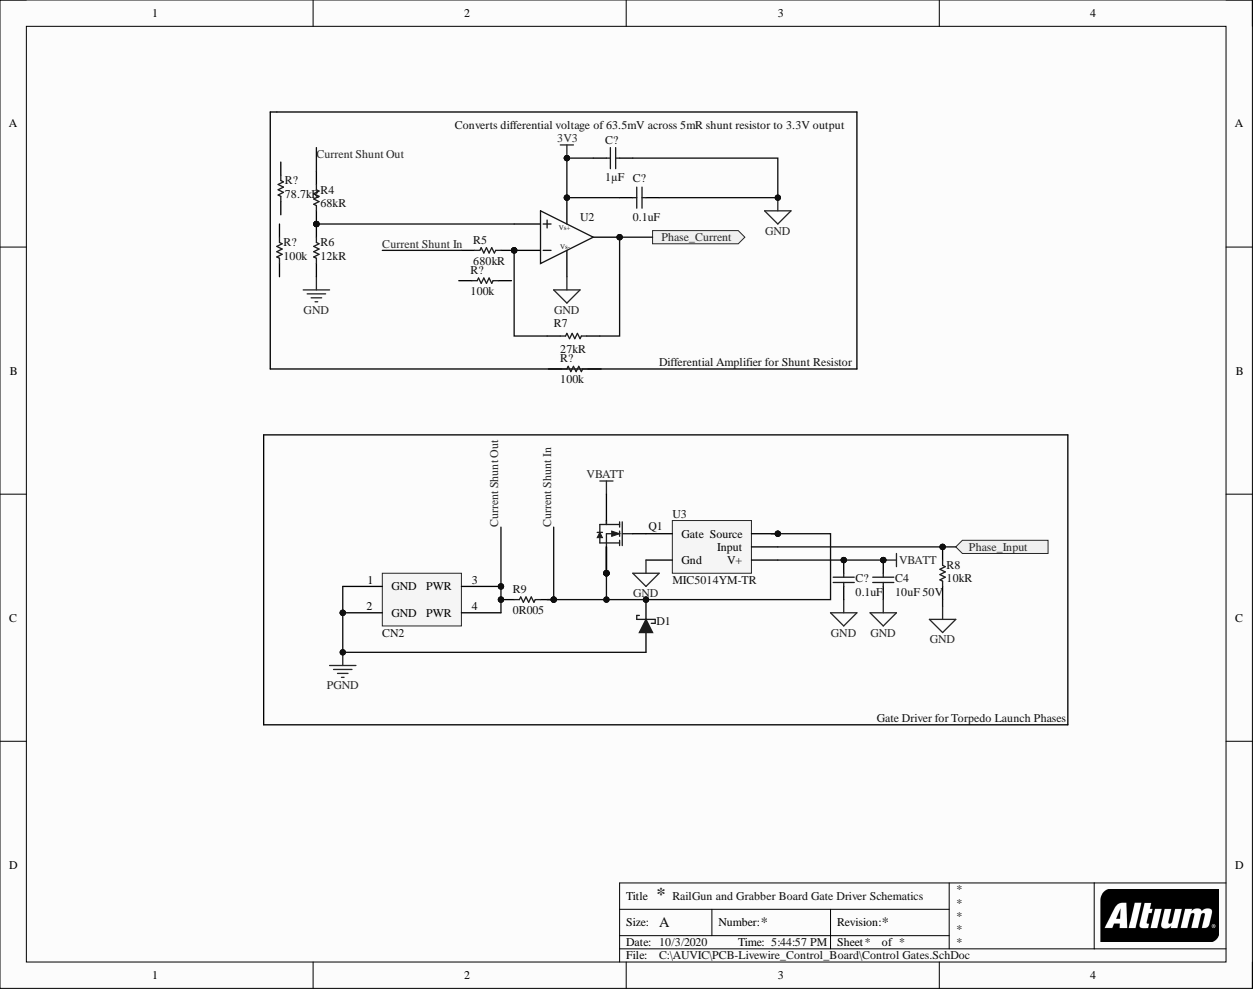
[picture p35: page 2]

Converts differential voltage of 63.5mV across 5mR shunt resistor to 3.3V output

Differential Amplifier for Shunt Resistor

Gate Driver for Torpedo Launch Phases

RailGun and Grabber Board Gate Driver Schematics

C:\AUVIC\PCB-Livewire_Control_Board\Control Gates.SchDoc

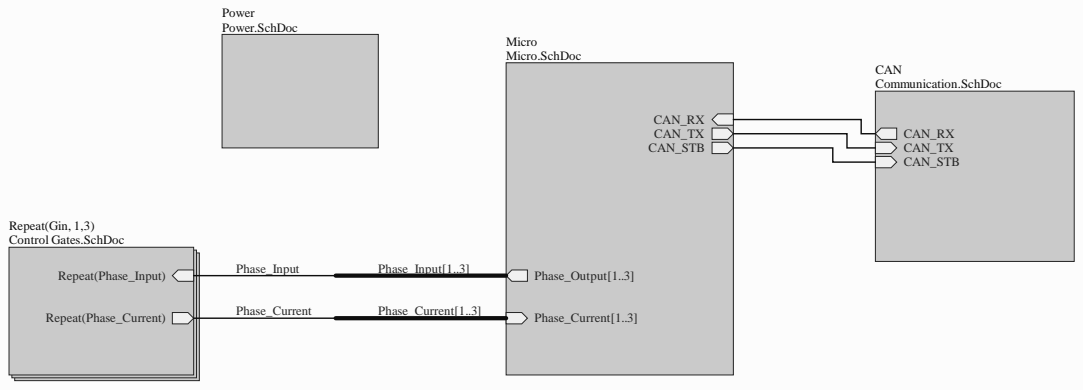
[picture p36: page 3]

C:\AUVIC\PCB-Livewire_Control_Board\Master.SchDoc

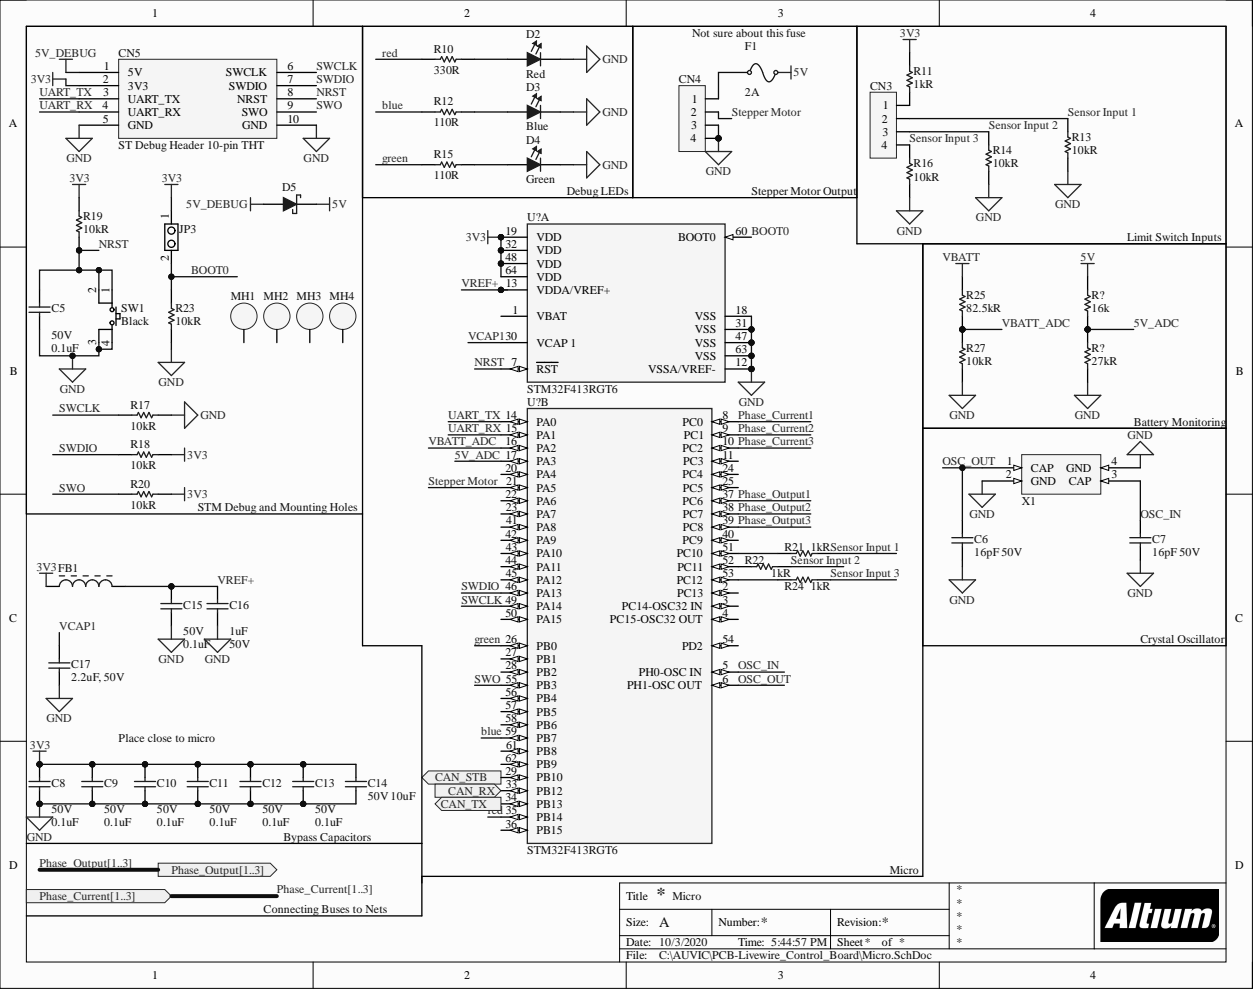
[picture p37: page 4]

Not sure about this fuse

ST Debug Header 10-pin THT

STM Debug and Mounting Holes

Place close to micro

Connecting Buses to Nets

C:\AUVIC\PCB-Livewire_Control_Board\Micro.SchDoc

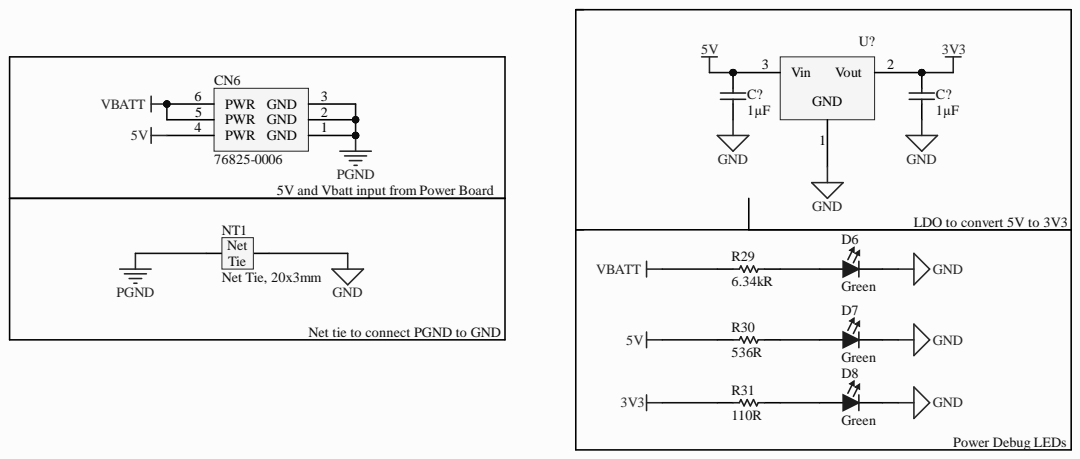
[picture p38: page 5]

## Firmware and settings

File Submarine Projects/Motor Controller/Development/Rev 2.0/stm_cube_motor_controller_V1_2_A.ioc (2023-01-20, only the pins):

Mcu.UserName=STM32F413VGTx
PE9.Signal=S_TIM1_CH1

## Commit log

2023-01-23 added JLC PCB Stackup and Rules submodule
    [0.0 - Rail Gun.PrjPcb, 16V_VBatt_External.SchDoc, 1700010106.stp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]
2023-01-23 Added PCBWay Stackup templates
